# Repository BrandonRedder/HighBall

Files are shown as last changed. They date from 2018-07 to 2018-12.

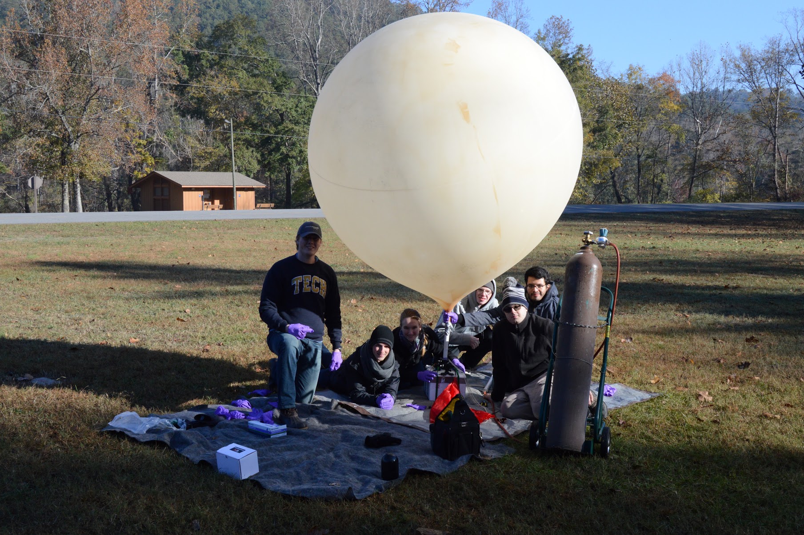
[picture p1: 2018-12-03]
Website/images/DSC_0252.JPG

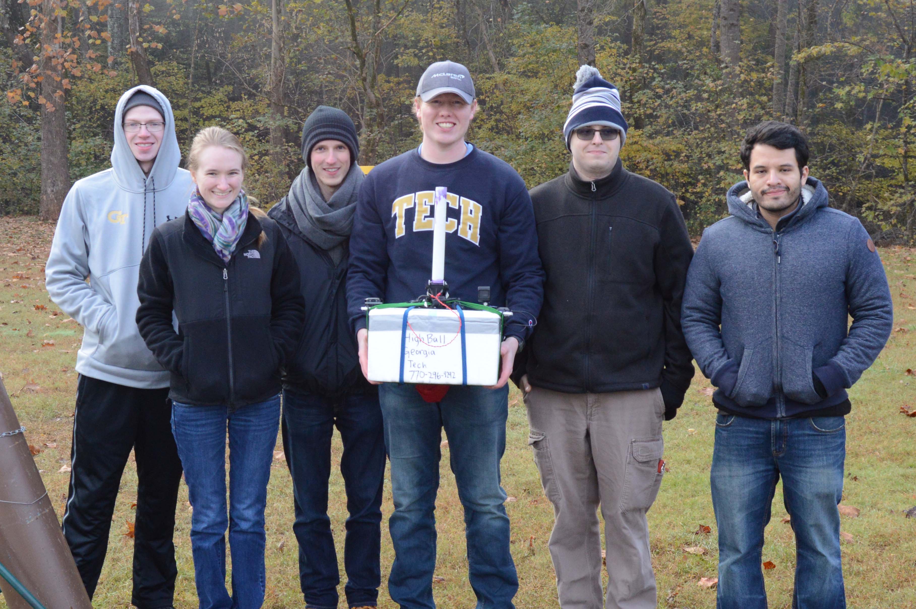
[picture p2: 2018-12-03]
Website/images/DSC_0246.jpg

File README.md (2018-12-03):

# High Ball  
The MITLL High Ball team’s directive is to design, launch, and control a high altitude balloon (HAB). A control system will use varying wind currents at different altitudes to adjust the balloon’s position. The High Ball team is requesting $1000 for development and testing of a viable HAB control system.

## Team Makeup
### Group Members  
* Mathew Manning
* Brandon Redder
* David Richardson
* David Sanchez
* Kristy Scott
* Kyle Watters

### Project Sponsor and Advisors  
**Sponsor:** MIT Lincoln Laboratories  
**Point of Contact:** Navid Yazdani  

**Primary Advisor:** Dr. Morris Cohen  
**Additional Advisor:** Dr. Whit Smith

## Project Goal
The goal of this project is to develop an altitude and location control system 
for a latex HAB to allow long duration flights over a general location. 
Algorithms take into account current pressure and temperature conditions when 
venting helium or dropping ballast to estimate altitude changes. This will
allow for inexpensive controlled balloon flights for a variety of payloads.

## Libraries
* Pressure Sensor (https://github.com/sparkfun/SparkFun_MS5803-14BA_Breakout_Arduino_Library)
* GPS (https://github.com/sparkfun/SparkFun_I2C_GPS_Arduino_Library)
* TinyGPS++ (http://arduiniana.org/libraries/tinygpsplus/)
* IMU (https://github.com/sparkfun/SparkFun_MPU-9250-DMP_Arduino_Library)

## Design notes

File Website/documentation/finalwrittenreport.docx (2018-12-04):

Autonomous Position and Altitude Control System for High Altitude Balloons

ECE4012 Senior Design Project

Section L03, High Ball

Project Advisor, Dr. Cohen

Manning, Mathew W, mathew@gatech.edu

Redder, Brandon A, brandonr@gatech.edu

Richardson, David K, drichardson42@gatech.edu, Team Leader

Sanchez, David, dsanchez36@gatech.edu

Scott, Kristine L, kscott43@gatech.edu

Watters, Kyle, kwatters6@gatech.edu

Submitted

2018 December 4

Executive Summary

The Georgia Institute of Technology in collaboration with the Massachusetts Institute of Technology Lincoln Laboratory developed a low-cost control system for high altitude balloons (HABs). There has been substantial interest in the application of HABs in communication and monitoring of regions not served by traditional infrastructure. Several examples include disaster recovery scenarios, rural areas, and active conflict regions. Many HAB designs suffer from short flight durations, prohibitive cost, or lack position control. The developed system employed a low cost altitude control system to increase flight duration. The payload weighed under six pounds to minimize the regulatory burden and allow the balloon to be operated during inclement weather conditions. In order to keep the design under the weight limit and improve structural stability, a novel cutdown mechanism was developed. To maximize flight duration and regional coverage, an altitude control system was developed using mechanical methods to release helium and ballast as well as a control algorithm. The control algorithm and ballast release have been demonstrated as functioning, but the helium release mechanism will need to be modified for future work. This altitude control could be used in conjunction with wind measurements to provide a position control system in the future. The development cost for the design was $77,117.24 with the cost of hardware per payload being $1,772.94.
Table of Contents

Executive Summary ii

1 Introduction 1
  1.1 Objective 1
  1.2 Motivation 2
  1.3 Background 2
2 Project Description and Goals 3
3 Technical Specifications & Verification 4
4 Design Approach and Details 5
  4.1 Design Approach 5
  4.2 Codes and Standards 17
  4.3 Constraints, Alternatives, and Tradeoffs 19
5 Schedule, Tasks, and Milestones 20
6 Final Project Demonstration 21
7 Marketing and Cost Analysis 25
  7.1 Marketing Analysis 25
  7.2 Cost Analysis 25
8 Conclusion 29
9 Leadership Roles 30
10 References 32

Appendices 36

Autonomous Position and Altitude Control System for High Altitude Balloons

1. Introduction

The MITLL High Ball team’s directive was to design, launch, and control a high altitude balloon (HAB). The control system utilized helium and ballast release mechanisms in order to adjust the balloons altitude. The High Ball team requested $1000 for the development and testing of a viable HAB control system.

  1.1 Objective

The goal of this project was to develop an altitude and location control system for a latex HAB to allow long duration flights over a general location. The control algorithm took into account the balloons altitude and vertical velocity to determine when to release helium or ballast. The altitude change due to dropping ballast was estimated using a simulation which employed the balloon’s lift force and payload weight. Weather forecasts from the National Oceanic and Atmospheric Administration provided wind speeds at distinct pressure levels allowing for prediction of horizontal movement over time [1]. This data was used to develop a model for the projected flight path under various control algorithms.

  1.2 Motivation

High altitude balloons offer a low cost solution for deploying RF and sensor packages. Traditionally, the flight time of an HAB is limited by the balloon bursting. Altitude control systems can drastically improve the flight duration resulting in a larger variety of applications. The presented control system will allow for prolonged deployment over a specific region.

Project Loon, a balloon system developed by Google, uses tennis court sized balloons to provide cellular service to low population regions. These balloons are capable of multi-month flights with both altitude and location control [2]. Although this system has proven to perform well, it is prohibitively expensive for many applications. A similar position control system deployed on a latex balloon will provide a low cost alternative.

  1.3 Background

As latex HABs rise, the decreasing air pressure causes the balloon to expand until the balloon bursts, ending the flight. Flight times are limited to approximately 3 hours. To overcome this hurdle, zero-pressure and super pressure balloons have been designed to increase flight durations. Both balloon types utilize polyethylene film which has a lower elasticity than latex to minimize expansion [3]. Zero-pressure balloons must drop ballast or vent helium to maintain altitude during diurnal cycles, and they can carry loads of up to 6,000 lbs for flights lasting 7-15 days on average [3]. Super pressure balloons rely on a thicker more rigid film material to limit expansion due to changing temperatures, and they can carry loads of up to 2000 lbs for flights lasting over 100 days [3]. For smaller organizations with instrument packages on the scale of 6 lbs these balloon options are unrealistic.

ValBal is a project out of Stanford that produced an altitude control system for latex balloons. The ValBal system holds the current world record for latex balloon flight duration, 121.5 hours [4]. The current design weighs approximately 2.5 kg without ballast and uses a 1500 g balloon with 9 kg of lift allowing the user to include 5 kg of ballast and instruments [4]. Each payload costs $1000 which makes it viable for a much broader range of users [4].

2. Project Description and Goals

The goal was to design a location control system to be used with HABs. Due to time constraints, the design was limited to controlling altitude and relying on the user to manually adjust for varying wind currents. The altitude control system consisted of pressure sensors for determining altitude as well as a mechanical release method for ballast and helium. Motion and location of the balloon was monitored through the use of GPS. An Arduino Mega 2560 was used for data processing and control of mechanical components. The system was deployed in a single payload so that an additional payload may be attached. The second payload could be used for RF or sensing applications. System features include the following:

- Physical control mechanism for helium and ballast release
- Altitude determination through pressure sensor calculations
- Position determination through GPS monitoring
- Manual control of HAB from ground station
- Autonomous HAB flight
- Recoverable payload
3. Technical Specifications & Verification

Table 1. Technical Specifications

Feature | Specifications | Measured Results
Operating Voltages | 3.3v, 5v | 3.3V, 5V
Battery Capacity | 21000 mAh | At least 3.5 hours
Payload Weight | 2500 g | 2245.282 g
Ballast Weight | 220 g | 340.194 g
Operating Altitude | 18 km to 27.4 km | < 4.5 km
Ambient Operating Temperature | -60℃ to 40℃ | Functional at -14.7℃ based on altitude
Internal Operating Temperature | -35℃ to 40℃ | 3.5℃ to 19.5℃
Operating Pressure | 1.0 to 1000.0 hPa | 589.0 hPa to 994.5 hPa
Maximum Recoverable Drop Velocity | 7 m/s | At least 4.27 m/s
Water Resistance | IPX4 | Untested
Flight Duration | 24 hours | 2.5 Hours

Table 2. Communications Specifications

Feature | Specifications | Measured Results
Latency | 5 seconds (for message <70 bytes) | 47.8 seconds
Maximum Usable Distance | Global | Confirmed at 25 miles

4. Design Approach and Details
  4.1 Design Approach
    4.1.1 Mechanical Design

Ballast Release

Ballast was dispensed via a rotary mechanism from the base of the payload. The dispenser assembly consisted of 3D printed parts which operated similar to a gumball machine. A 3D rendering of the design is shown in Figure 1. A set amount of ballast first moves from a chamber in the payload to the hopper. The hopper is then rotated 90° causing the ballast to fall out of the hopper. This rotation also allows ballast to fill the next section of the hopper to be used for the next release. This mechanism prevents a direct connection from the ballast chamber to the exterior of the payload. The hopper was connected to a servo which controlled the number of rotations.

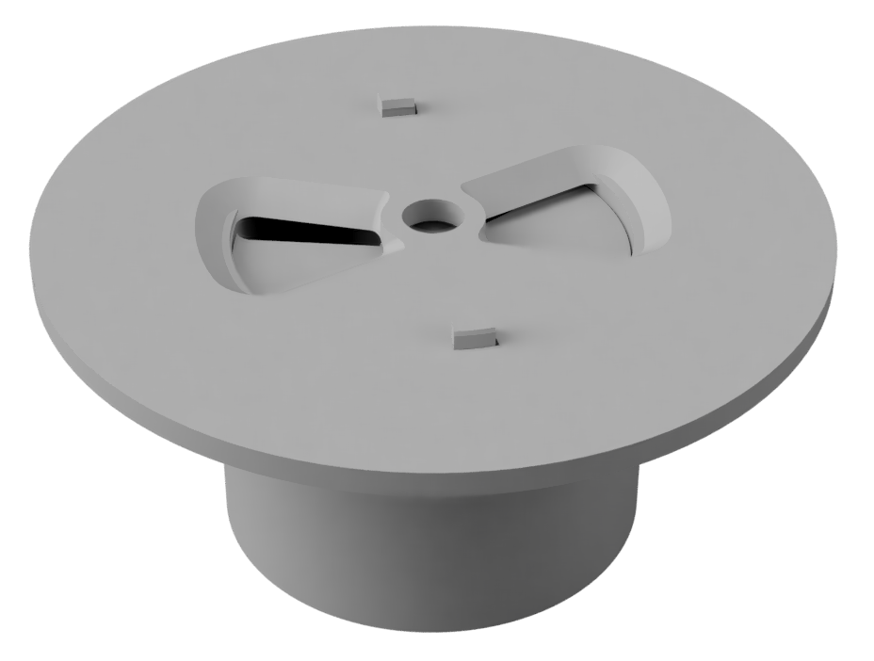
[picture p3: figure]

Figure 1. 3D rendering of the ballast dispenser assembly

Helium Venting

Traditional HABs are connected to their payload by a long cord, but this prevents helium from being released from the balloon. The payload was mechanically connected to the balloon via PVC pipe attached to a mounting bracket on the top of the payload. The balloon was attached to the PVC pipe using zip ties. The PVC is attached to the mounting bracket using an adaptor with two protruding fins that are locked into place by clamps on the mounting bracket. These clamps are held in place using nylon cord. A rubber stopper attached to a spring at the bottom of the bracket blocks the adapter vent to prevent helium from escaping during normal operation. The assembly can be seen in Figure 2. The stopper is attached to a servo located within the payload by a thin rod allowing the servo to open or close the vent. During the flight, a leak was developed. It is uncertain the exact cause, but some potential causes are as follows:

1. The mount and stopper were slightly porous to helium. Helium is a very difficult gas to trap successfully, so it is possible the 3D printed parts were allowing the helium to leak through them.
2. The stopper was not fully sealed against the opening allowing small amounts of gas to escape over the duration of the flight. Once the balloon was attached, it was impossible to check if the stopper was pressed firmly against the opening.
3. There was a non-stopper related hardware failure. This could include the connection between the balloon and the PVC allowing helium to escape, or small cracks in the PVC or mounting bracket.

Further examination and testing is required to determine the exact cause of failure. This is a key flaw in the design that needs to be addressed in future work.

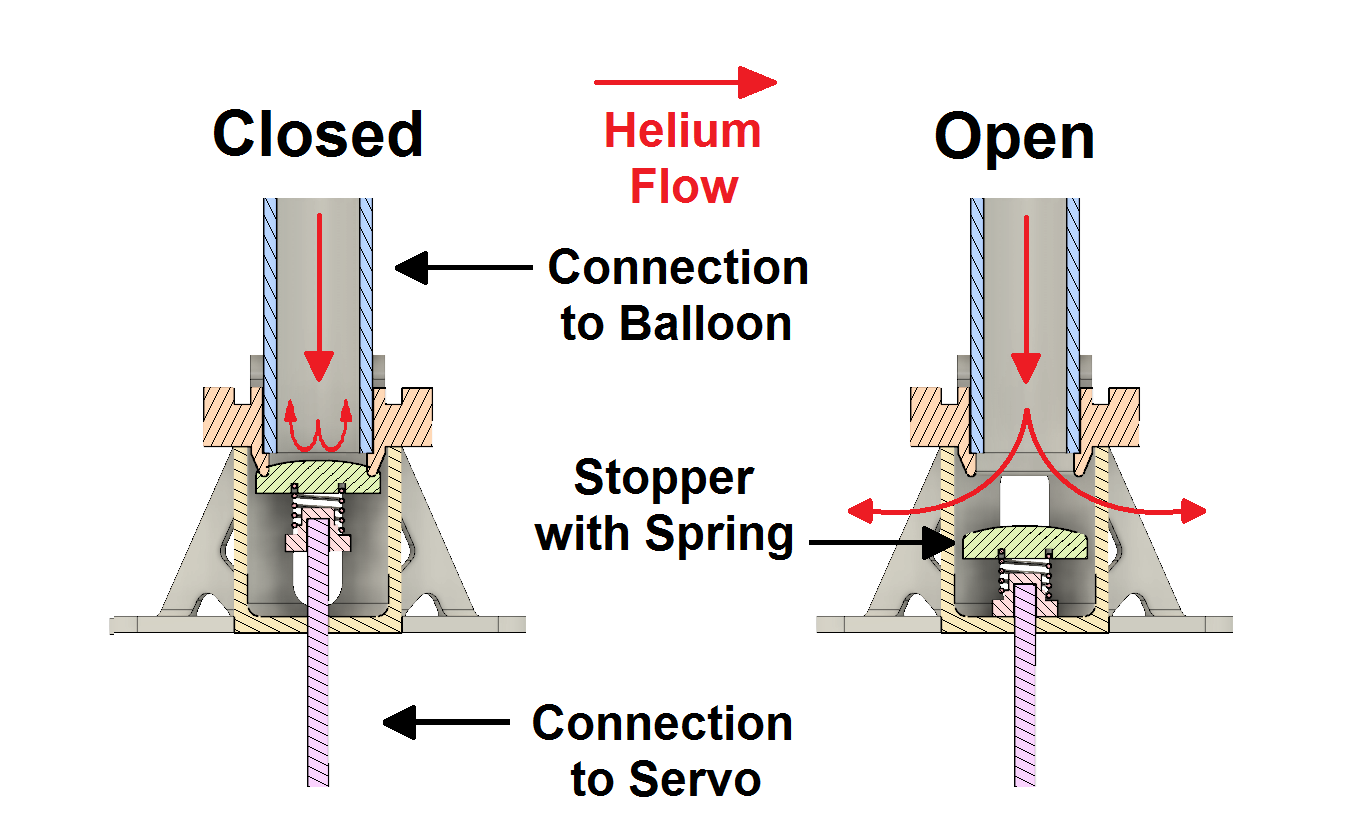
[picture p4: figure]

Figure 2. Helium Venting System

Cutdown

The balloon was rigidly connected to the payload through the helium venting assembly described above. This connection was held in place with a small section of nylon cord as discussed above. Nichrome heater wire was wrapped around the cord similarly to a solenoid. This wrapping can be seen in Figure 3.

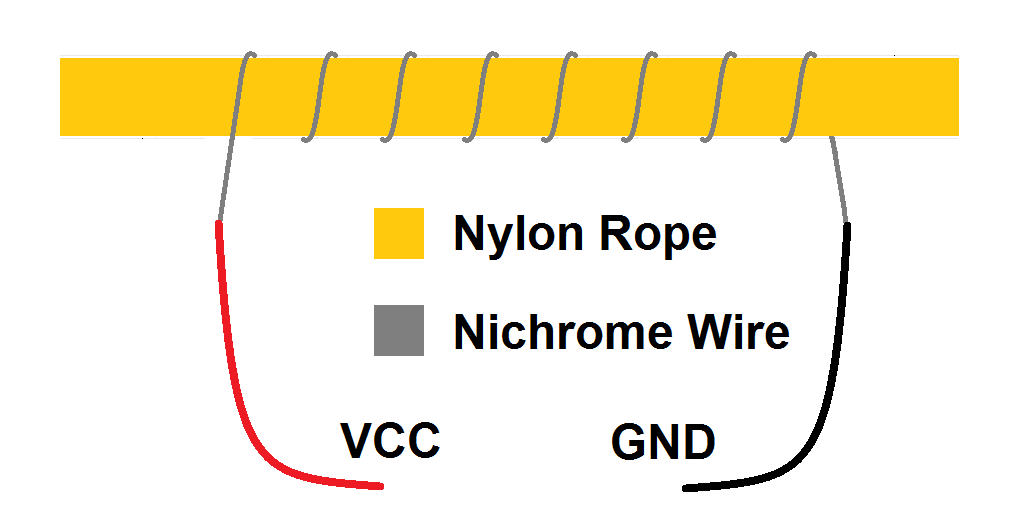
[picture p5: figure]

Figure 3. Nichrome wire wrapped around nylon cord

When the cutdown command is given, the controller biases an N-channel mosfet driver energizing the nichrome wire. This bypasses the voltage regulation circuitry and provides a direct connection from the battery to the nichrome. To control current, the driver is connected to a pulse width modulation pin on the controller. This mechanism, shown in Figure 4, was tested prior to launch and shown to work under the weight of the payload while empty. A video of this test can be seen in Appendix A.

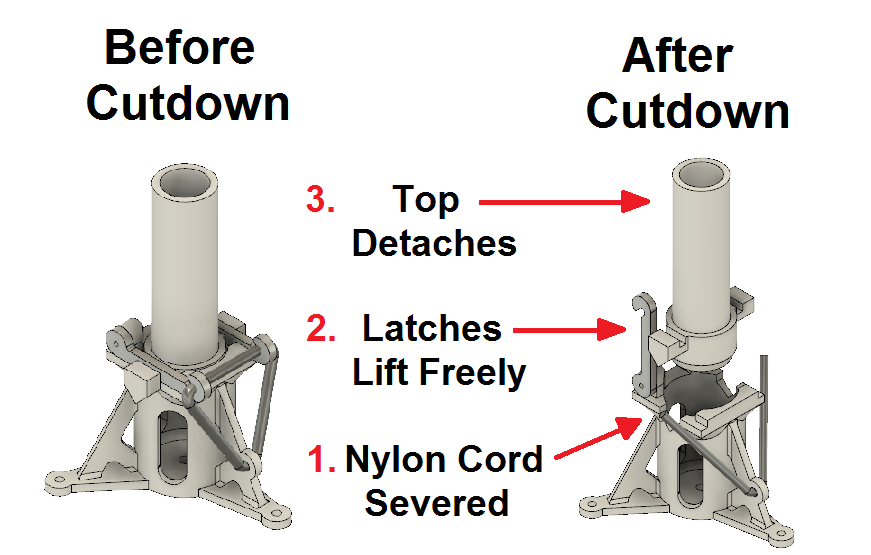
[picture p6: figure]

Figure 4. Cutdown Mechanism

Parachute Deployment

Due to the direct connect between the payload and the balloon, the traditional method of an inline parachute was impossible. The parachute was instead attached to the helium release mounting bracket. With no method of keeping the parachute above the payload, it will fall below and begin to fill with ballast as it is released. To counteract this, a carbon fiber rod was attached to the top of the payload. The parachute was then held to this rod via a plastic loop on the top of the parachute. This prevents the parachute from trailing under the payload while still allowing the parachute to deploy. A video of the drop test can be seen in Appendix A.

    4.1.2 Electrical Design

Communication

Communications between the balloon and the ground station are facilitated through the Iridium satellite network by the RockBlock 9603, a breakout board utilizing the Iridium 9603 satellite transceiver. The breakout board utilizes four communications pins to interact with the microcontroller. The first two pins are RX and TX connections to allow messages to be sent to and from the device. The other 2 pins allow the RockBlock board to be placed in a low power state to preserve energy and to inform the microcontroller when a new message has arrived. The module uses an external 1621 Mhz patch antenna to communicate with satellites [5]. Outgoing messages are rerouted through nearby satellites before being sent to an Iridium ground station where the message is sent via an email attachment to the user [5]. Incoming messages are uploaded as an HTTP POST to the RockBlock website before being sent back through the same channels to the transceiver.

Microcontroller

The microcontroller used was the Arduino Mega 2560 development board (based on the ATmega2560). It was selected due to being available from the previous development team. It fit the communication and use requirements for managing the payload. Using a smaller board is possible if size or weight becomes a significant limiting factor, but at only 37g, the Arduino mega is not a significant source of weight [6]. The microcontroller is connected to the remainder of the electronic components via a custom PCB.

Sensors

Several sensors were used to provide data to the controller. In addition, some sensors were removed from the design due to technical constraints. The code for reading the data from the sensors is included in Appendix B (Sensors.cpp and Sensor.h). Each of the sensors are summarized below.

GPS Module

The GPS module used was the SparkFun XA1110 GPS [7]. This module was selected specifically due to its “balloon mode” which allows it to continue functioning above 65,000 feet. This was the primary method of monitoring the position of the balloon.

The GPS altitude is also sent to the ground station and displayed on the graphical user interface (GUI). This altitude was not used in the control algorithm due to the limitations of GPS altitude measurements [8]. Instead the altitude measured from the altimeters was used.

Altimeters (2x)

The altimeters used were the SparkFun Pressure Sensor Breakout - MS5803-14BA [9]. This sensor was selected due to the ease of integration, and its pressure range of 0-14 bar with a minimum resolution of 0.2 mbar. At altitudes of 70-90 thousand feet, the atmospheric pressure is 17.6-44.9 mbar [10]. Since altitude determination was the basis of the control algorithm, two altimeters were included in the design to mitigate any potential for sensor failure. Due to time constraints, no sensor failure detection was implemented in the code. Instead, the measurements from the two sensors were averaged. Future work should include more robust failure detection which can be done by comparing to the GPS altitude or an expected value.

Temperature Sensor - Removed

The temperature sensor initially specified in the design was the TI LM335Z/NOPB [11]. This sensor was specified due to its range overlap (-40 to 100 °C) with the temperatures expected at altitude. Originally, the temperature sensor was to be used as a control for an internal heating element. To preserve battery and reach the desired temperature the heater was going to be turned on and off. It was ultimately removed from the design as the electronics were estimated to produce enough heat to stay within the operating temperature range. For monitoring of the payload conditions, temperature data was sent to the ground.

During testing, the temperature sensor was reading inaccurate and inconsistent data. This may have been due to a hardware fault earlier in the semester, but the cause of failure was not determined. This led to the removal of the temperature sensor from the design. In its place, the pressure sensors’ built in temperature sensors were used which have an accuracy of ±0.8℃ [9]. For internal temperature monitoring, this was determined to be sufficiently accurate; however, if future work needs more accurate temperature measurements, a dedicated temperature sensor should be added back to the design.

Inertial Measurement Unit (IMU) - Removed

The IMU initially specified in the design was the SparkFun 9DoF Razor IMU M0 [12]. This sensor was intended to be used to calculate acceleration both normal and tangential to Earth as well as provide a check for the altitude and position measurements. Unfortunately, the selected IMU presented significant software challenges. While an IMU provides valuable information for position monitoring, future designs should use a different IMU. The issues with the presented IMU are outlined below:

1. The x, y, and z axes for the acceleration measurements differed from what was printed on the board. Per the datasheet, the axis orientation for the compass outputs differs from that of the accelerometer and gyroscope outputs, and the printed axes correspond to the compass. To avoid confusion, the following changes were made to the acceleration outputs to match the axes printed on the board: x acceleration to the y axis, y acceleration to the x axis, and z acceleration to the -z axis.
2. The provided repository for the chip had errors calculating roll, pitch, and yaw. This required changes to the firmware on the internal microprocessor to account for these differences. The current state of the firmware is shown in Appendix C.
3. Communication between the IMU on-board Arduino and the primary Arduino MEGA was unsuccessful. This is what led to the IMU’s removal from the final design.

In addition to the above mentioned issues, future work should aim to make the code robust to initial position upon powering on the IMU. The sensor outputs are relative to the initial position rather than absolute measurements. The current design requires the IMU be in a specific orientation when turning on. The IMU must be level with the x axis pointing north for determining the vertical and tangential directions respectively. Future designs should use the acceleration due to gravity to find the true vertical direction and the magnetometer to find the true tangential direction. This will provide more accurate data and prevent any errors due to misalignment when turning on the device.

    4.1.3 Software

Ground Station Interface

The ground station interface consists of a GUI which allows the user to compile new messages, view previously sent messages or received messages, and view real time graphs of received data. As the payload sends messages to the ground, that information is retrieved automatically and the GUI displays an incoming message notification. Each new message contains the balloon’s GPS coordinates, altitude, interior temperature, and pressure measurements along with current software settings. Outgoing messages contain specifications for the altitude control algorithm and manual commands for venting helium, dropping ballast, and cutting down the payload. The layout of the main GUI tab can be seen in Figure 5. For brevity, the layout of each page of the GUI and the code for the GUI can be found in Appendix D and E respectively.

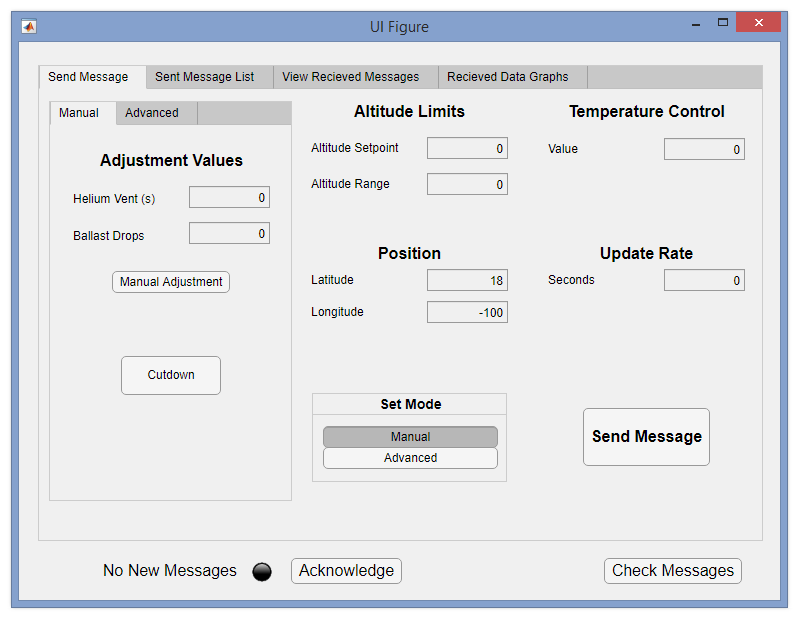
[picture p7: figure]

Figure 5. GUI Main Page

Altitude Control

The altitude control system was separated into three subsystems, the helium release, the ballast release, and the autonomous control loop. The software for the helium and ballast release can be seen in Appendix B (Actuators.cpp and Actuators.h). To control the helium and ballast release, servos were rotated a specified amount to either open/close the helium vent or release a set of ballast. These functions could be triggered either by the autonomous control or by communication from the ground station. The code for the autonomous control loop can also be seen in Appendix B (Control.cpp and Control.h). Both the altitude and vertical velocity were weighted in order to determine when to release helium or ballast. These weights were determined using a simulation. Initially, the algorithm was intended to use the vertical acceleration found by the IMU, but due to the removal of the IMU, the vertical acceleration was also removed. A simulation of the control algorithm showed that the removal of the vertical acceleration had a negligible impact on the effectiveness of the algorithm.

Issues and Considerations

In its current state, the payload must be launched in manual control mode. This is because the altitude control loop has no guard on releasing ballast if the balloon was just launched. As a proof of concept, this functionality works, but future work should aim to allow for fully autonomous flight from launch to landing. A similar guard should be placed on the helium release while the payload is falling in order to reduce battery consumption.

Future work can also be done to improve the control loop. The weights for the different parameters can be optimized based on measured helium release rates. There may also be additional parameters that play a key role in how the balloon operates such as temperature or wind conditions that are not currently accounted for. Additionally, for longer flights, it may be possible to use the natural warming and cooling of the atmosphere to prolong the flight.

Iridium Communication

Messages to and from the balloon are in the form of a segmented binary vector. Each segment is a predetermined length and represents a different parameter. To limit overall data usage the minimum and maximum values of each parameter were determined along with the resolution of the sensors involved. This allows the parameter to be represented as an integer value with the following formula; Encoded =Round((Value - Minimum)/(Resolution)) . The encoded value will be an unsigned integer with a minimum value of 0 and a known maximum value, meaning only N bits are needed to store the value without losing precision given Maximum ≤ 2^N . Figure 6a shows the layout of messages sent to the payload and Figure 6b shows the layout of messages received from the payload. Functions were developed for both the microcontroller and the ground station to encode and decode messages using this predetermined structure. The code for the communication can be seen in Appendix B (Communications.h and Communications.cpp).

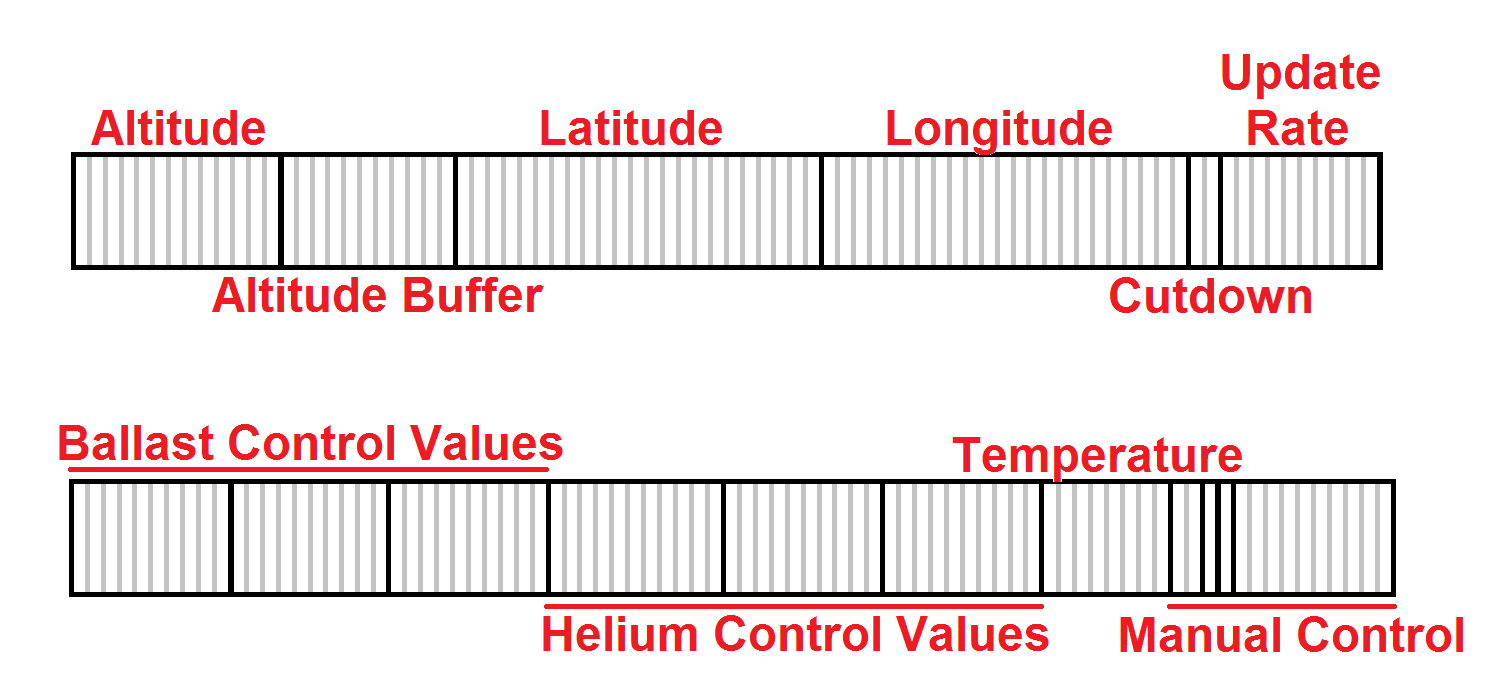
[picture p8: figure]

Figure 6a. Message Structure from Ground to Payload

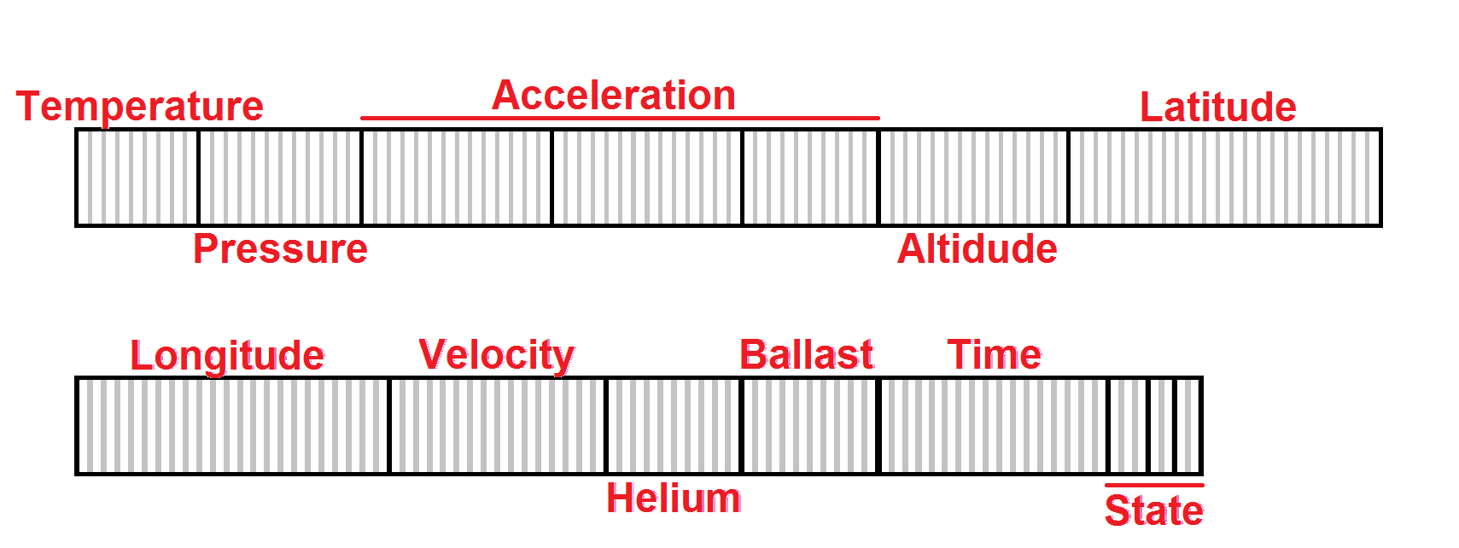
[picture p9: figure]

Figure 6b. Message Structure from Payload to Ground

Flight Simulation

Current HAB flight simulation tools operate on the assumption that the balloon rises until it pops then begins falling. This does not provide an accurate model when the payload is actively preventing the balloon from reaching the altitude at which the balloon pops. To circumvent this, a flight simulation tool was developed. This model utilizes weather data from the Global Forecasting System [1] to determine the wind conditions, pressure, humidity, and temperature at a given time and position. The data is used to determine the buoyancy, drag, and gravitational forces acting on the balloons given the current velocity, mass of the payload, and mass of helium in the balloon. These forces allow the balloon’s instantaneous acceleration to be approximated over time, even when changes to the system occur during helium venting or dropping ballast. The simulation outputs the ambient weather conditions, position, acceleration and velocity of the payload which can be viewed graphically. The simulation ends when the payload reaches the ground or when a preset time is reached. While the simulation cannot account for all variables, it allows the user to approximate how the balloon’s trajectory will change in response to the altitude control system. This was utilized to determine appropriate variables for the control algorithm. The full flight simulation code can be seen in Appendix F.

Temperature Control

Temperature control was omitted in the final design due to the short expected duration of the flight. For short flights, the heat generated by the electrical components provides sufficient heat to keep the interior temperature above the operating range. This may not be the case for longer duration flights. If that is the case, a heating element can be added to the design to maintain the internal temperature.

Wind Detection

Due to time constraints, wind detection was not implemented in the design. This prevents the design from autonomously adjusting position, but it is still possible through manual changes from the ground station. This requires the person at the ground station to determine the wind conditions from the available data and correctly send helium or ballast release commands. Future work should aim to determine wind direction on board to allow for autonomous position control. This may require an IMU to monitor the payload’s orientation and horizontal acceleration.

  4.2 Codes and Standards

FAA Title 14 - Part 101 - Subpart A (Appendix G) describes the conditions under which unmanned civilian vehicles may be operated within the United States. Part 101.1 specifies that any unmanned free balloon must comply with subpart D with the exception of balloons that:

- Carries a payload package that weighs more than four pounds and has a weight/size ratio of more than three ounces per square inch on any surface of the package, determined by dividing the total weight in ounces of the payload package by the area in square inches of its smallest surface
- Carries a payload package that weighs more than six pounds
- Carries a payload of two or more packages that weighs more than 12 pounds
- Uses a rope or other device for suspension of the payload that requires an impact force of more than 50 pounds to separate the suspended payload from the balloon

The regulations in Subpart D (Appendix H) directly interfere with the intended application of the system, so the payload is designed to comply with the exceptions listed in Part 101.1.

Part 101.7, as it applies to unmanned free balloons, prohibits the operation of the balloon in a manner that may be hazardous to other persons, or their property. It also prohibits dropping any objects, if such an action creates a hazard [13].

FCC Title 47 - Part 97.113 lists prohibited transmissions on amateur radio wavelengths. Relating to this project, no station shall transmit communications for hire or for material compensation, direct or indirect, paid or promised, except as otherwise provided in these rules [14]. This regulation makes amatueur radio an unsuitable means of communication for the system due to the commercial nature of the project.

FCC Title 47 - Part 22.925 prohibits the use of cellular phones while airborne, preventing the system from using a cellular phone to communicate with the payload during flight [15].

The Iridium 9603 transceiver utilized in this design has been granted authorization by the FCC as a Licensed Non-Broadcast Station Transmitter under the conditions listed in FCC Title 47 - Part 25 [16]. The grant of equipment authorization requires that the transmitter be installed to provide 20 cm of separation distance from all persons, and must not be operation in conjunction with any other transmitter within a host device [17].

  4.3 Constraints, Alternatives, and Tradeoffs

Due to FAA regulations, the payload weight must be less than 6 lbs [13]. This restriction resulted in a tradeoff between component selection and ballast weight. Maximizing the amount of ballast is important for increasing flight duration, but longer flights require a larger power supply. The structure for the payload also contributed to the weight because it had to be sturdy enough to hold the cutoff mechanism for the balloon and provide insulation. Though greatly reduced through iterative design, the weight of this housing was a large portion of the total weight. The current design opted to increase structural rigidity instead of increasing flight duration. This decision was made to improve the chances of payload recovery, and to show a proof of concept for the altitude control mechanisms.

Due to the altitude of HAB flights, the system must be able to sustain operations in temperatures as low as -60° C. Many electronic components fail at this temperature, so special considerations were taken into account when designing the payload. The enclosure used was insulated so that less heat would be lost, and the heat generated by the electronics on the inside helped maintain internal temperature. The heater originally proposed was not used due to reasons discussed in Section 4.1.3. The test flight did not reach an altitude at which the internal temperature could be tested, so it is not currently known if a heater is necessary. The payload remained in the operating temperature during the test flight. The lowest recorded internal temperature was 3.5℃, measured while the lid was open prior to launch. During the flight, the internal temperature steadily rose due to the heat generated by the electrical components.

5. Schedule, Tasks, and Milestones

The GANTT and PERT chart are shown below in Appendix I and J respectively.

Brandon Redder performed the majority of the payload hardware design and assembly. He also did the PCB design and fabrication. The hardware assembly was a critical element, and the last thing completed on the critical path. Mathew Manning helped Brandon with hardware assembly and testing. Mathew’s tasking played an important role in meeting deadlines and ensuring all elements of the hardware were functioning. David Richardson wrote and maintained the control algorithm and all the sensor interfaces except the IMU. He assisted with the IMU calculations, and worked on the communication between the main Arduino and the IMU. Additionally, he was involved in the testing and debugging of both hardware and software. These tasks were on the critical path and were of medium complexity. The primary source of difficulty was with the IMU communication and software debugging. Kristine Scott wrote the firmware for the IMU to calculate acceleration and orientation values. She also assisted with software, and communication debugging. Although the IMU was removed from the design, it was a difficult task that took a significant amount of time. Her assistance with debugging was also important to the launch of the payload on time. David Sanchez developed the day of launch checklist, as well as determining a location to launch from. While this tasking was fairly simple, it took time and was one of the most important tasks of the project. He also played a significant role in the cutdown code and testing as well as debugging of the software. His testing of the GPS caught a significant error in the code that would have resulted in data loss at high altitude. Kyle Watters wrote both the simulation and communication code for the project. Communication with the payload was one of the most critical features of the design, as without it there would be no way to test any of the other design elements. This in conjunction with the simulation code posed a moderately difficult task that took a considerable amount of time. The main loop was written by David R., Kristine, David S., and Kyle. This was the most critical piece of software in the design but was of relatively low difficulty.

6. Final Project Demonstration

The final project demonstration was done in two parts, in flight reporting and ground testing. The following specifications were demonstrated during and immediately prior to the flight:

- The hardware was operating at the specified 3.3V and 5V.
- The time from powering on to payload recovery was 3.5 hours which demonstrated a minimum estimate for battery capacity.
- The payload weight was measured to be 2245.282 g which is below the 2500 g limit. This allowed the ballast weight to exceed its specification at 340.194 g.
- The altitude reached 4.5 km during the flight which falls well below the desired range of 18 km to 27.4 km. This was due to a helium leak likely due to a hardware failure as discussed in the Helium Release subsection of §4.1.1. A plot of the altitude vs time can be seen in Figure 7.
- The minimum ambient operating temperature experienced during flight was -14.7℃. Testing at the minimum specified temperature was impossible to the previously mentioned maximum altitude falling below the expected altitude.
- The operating temperature during the flight ranged between 3.5℃ and 19.5℃ which was within the required range. The temperature was shown to increase over the duration of the flight as shown in Figure 8. This indicates the payload may be able to self regulate temperature without an internal heating element.
- The minimum pressure experienced during the flight was 589.0 hPa. The payload remained operational at this pressure, but pressures below that were unable to be tested. A graph of the pressure vs time can be seen in Figure 9.
- The drop velocity was measured to be 4.27 m/s and the payload was fully functional after recovery. This velocity was calculated from the altitude vs time graph shown above in Figure 7.
- Water resistance was untested as it was deemed unnecessary for the initial prototype
- The flight duration accomplished was 2.5 hours.
- Latency was measured to be 47.8 seconds.
- The usable distance for the payload communication was confirmed to be at least 25 miles from the ground station and was consistent when the payload was in view of satellites. After the payload left the ground, the communication was more consistent and reliable than it was on the ground. This is thought to be because there was less blocking the view of the payload.
- The ballast release mechanism was shown to work after the payload had landed, prior to recovery. It was impossible to see if ballast was released during the flight due to a helium leak, but the post landing tests showed that it was working through remote communication.
- Helium release was shown to have an impact on the buoyancy of the balloon and it was shown that the blocking method was not fully functional from the path that the flight took. The effects of this leak can be seen in Figure 7 where the altitude follows the path expected of a continuous loss in lift.

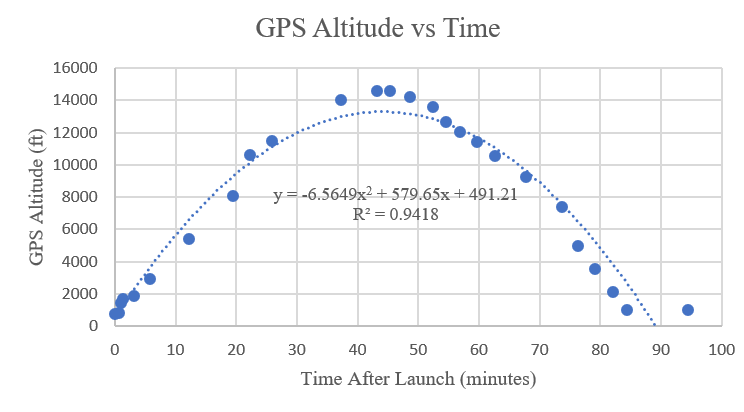
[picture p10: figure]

Figure 7. Plot of balloon altitude vs time from the test flight

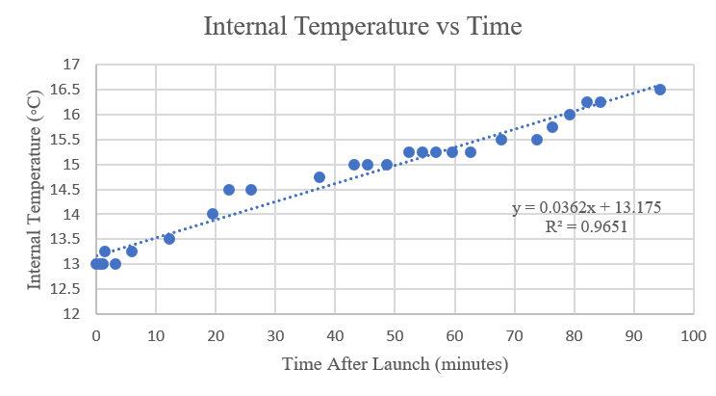
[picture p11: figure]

Figure 8. Plot of payload temperature vs time from the test flight

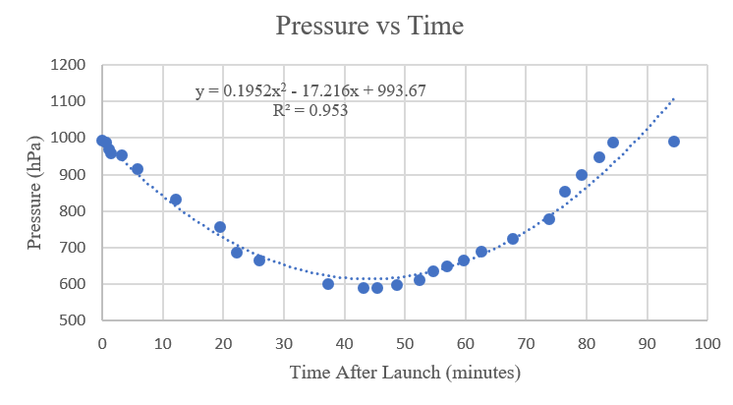
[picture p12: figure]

Figure 9. Plot of pressure vs time from the test flight.

Ground testing demonstrated the functionality of the payload and is as follows:

- The parachute deployment method was tested by a four story drop test. A video of the drop can be seen in Appendix A.
- The cutdown method was tested iteratively so that the best wrapping method for nichrome wire could be determined as well as the effects of cutdown on the other electronic components. The method of wrapping can be seen in the Cutdown subsection of §4.1.1 and the current draw was not enough to affect the other components.
- Ballast dispensing was demonstrated both on the ground and during the flight. The dispensing mechanism was tested on the ground and can be seen in a video in Appendix A.
- The helium venting mechanism was demonstrated to work mechanically, but from the launch, it was shown to be ineffective at blocking the release of helium.
- The physical functionality of the payload demonstrated the functionality of the software and communications. The data being taken can be seen in the logs in Appendix K.
7. Marketing and Cost Analysis
  7.1 Marketing Analysis

It is not plausible to launch an HAB project at the same scale as Project Loon unless adequate funding is acquired [2]. Stanford University's ValBal team developed a low cost alternative. The ValBal project utilized less than $1,000 to achieve the longest recorded latex balloon flight. The Stanford team’s aircraft used an altitude control system to extend the flight duration [18]. In addition to altitude control, the proposed design aimed to develop a position control system. Though the project did not demonstrate autonomous position control. Changing altitude with known wind directions will allow for directed changes in position. The presented work could be easily built upon to develop an autonomous position control system.

The ValBal design exceeds the weight limit specification which requires users to follow FAA regulations 101.33, 101.35, 101.37, and 101.39 [13] [18]. The proposed design weighed less than six pounds which will allowed for an additional six pound payload without needing to follow the above FAA regulations. Of particular importance, the proposed system may be operated during inclement weather conditions without prior notice to the FAA [13].

  7.2 Cost Analysis

7.2.1 Hardware Costs

The HAB control system consisted of electronic, mechanical, and structural components. The previous design effort purchased some supplies that were reused shown in Table 3. These items are listed separately because they were purchased by the previous team. They were included in the final cost calculations.

Table 3. Previous Supplies

Item | Estimated Cost
Arduino Mega 2560 | $38.50
5 ft Diameter Parachute | $50
1200 g Latex Balloon | $120
RockBLOCK Iridium Module | $250
Servos | $80

The additional parts necessary to build the design are listed in Appendix L. The listed components provide enough materials for a single launch. Additional launches will require new balloons and potentially hardware if the payload is unrecoverable.

In addition to hardware, the satellite communication in use requires a data plan with monthly costs and additional charges to purchase credits as shown in Table 4. The credits are needed to send or receive messages with each action costing 1 credit.

Table 5 shows the cost of each of the individual subsystems. An entire bill of materials is included in Appendix L.

Table 4. Communication Data Plan Charges

| Cost per each | Quantity
Monthly Subscription Fee | $12.75 | 3
200 Credits | $25.50 | 1
1000 Credits (Bundle Discount) | $102.02 | 1
Total Cost | $165.78

Table 5. Subsystem Costs

Project Subsystem | Cost
Payload | $231.84
Helium | $250
Electrical System | $371.88
Cutdown | $126.71
Communications | $611.07
Ballast | $181.75
Total | $1,772.94

7.2.2 Development Costs

The design team will consist of six engineers. Table 6 shows the number of work hours per engineer estimated for the duration of the project.

Table 6. Number of Work Hours per Engineer

Task | Hours
Sensor Integration | 13
Algorithm Development and Implementation | 28
Research | 5
Meetings | 15
Parts Fabrication | 15
Assembly | 20
Ground Testing | 10
Launches and Launch Preparation | 15
Presentation | 2
Reports | 12
Total | 135

Each engineer is estimated to have a salary of $65,000, per year [19]. The United States Office of Personnel Management defines one work year as 2087 hours [20]. Using these estimates, the hourly rate of a single engineer is $31.15. A fringe benefit rate of 31.9% and an overhead rate of 120% are assumed [21]. The total development costs under these assumptions are shown in Table 7.

Table 7. Total Project Costs

Project Section | Cost
Parts | $1,607.16
Communication Costs | $165.78
Labor | $25,231.50
Fringe Benefits (31.9% of Labor) | $8,048.85
Subtotal | $35,053.29
Overhead (120% of Subtotal) | $42,063.95
Total | $77,117.24

8. Conclusion

In its current state, the payload is capable of releasing ballast based on manual or automatic control schemes. The helium release mechanism allowed helium to leak over the duration of the flight. While this does demonstrate that the opening was large enough to vent sufficient gas to reduce altitude, it is a significant design flaw that needs to be addressed in future work. In order for the payload to adequately control altitude, a method for preventing the helium from venting unintentionally must be developed. Testing of the control algorithm was also limited due to time constraints and insufficient test flight data. Since the test flight only reached approximately 4.5 km, there was not enough data gathered to provide an accurate model for how to control the balloon. Future flights would provide valuable feedback on how the current control algorithm performs, as well as where potential improvements can be made.

During the development of the payload, certain errors were made that should be avoided during future work. Of particular note, was the selection of an IMU with a separate on board Arduino, and the milling of the custom PCB. Due to the on board Arduino, the team was unable to get communication between the IMU and the main microcontroller. This made determining vertical acceleration impossible which limited the data available to the control algorithm. The removal of the IMU also prevented checking the altitude and position data against the IMU’s acceleration and rotational data as discussed in the initial proposal. In the future, an IMU that connects directly to the main controller would be easier to communicate with and use. When milling the PCB, multiple shorts were developed. This ultimately led to the failure of the GPS and IMU sensors. These components were replaced, but in the future, any PCBs should be examined closely to prevent this from happening. Having the PCB milled by a professional board house would likely reduce the chances of this happening again.

9. Leadership Roles

Brandon Redder was responsible for maintains the group’s website as the webmaster. He also led hardware assembly. Mathew Manning led the recovery team after the payload landed. He also played a key role in the hardware assembly and testing. As team leader, David Richardson oversaw communication between the team and advisors. He provided direction and made final decisions regarding both hardware and software design elements. He is also the expo coordinator for the team. Kristine Scott led the integration of the different sensor elements. She was also the documentation lead, meaning she was responsible for ensuring all documentation was submitted in a timely manner. David Sanchez oversaw pre-launch preparation. This included launch site selection, pre-launch checklists, and ensuring all necessary items were brought to the launch site. He was also the primary contact for the cutdown software implementation. Kyle Waters oversaw both the simulation and satellite communications. In this role, he developed models for the balloon’s flight path, and used this to help define control parameters. He was also responsible for all communication between the payload and ground station.

10. References

[1] National Oceanic and Atmospheric Administration, “Global Forecast System (GFS),” July 14, 2018. [Online]. Available: (https://www.ncdc.noaa.gov/data-access/model-data/model-datasets/global-forcast-system-gfs)https://www.ncdc.noaa.gov/data-access/model-data/model-datasets/global-forcast-system-gfs [Accessed: July 20, 2018].

[2] X Development LLC, “Technology,” Project Loon, 2018, [Online]. Available: (https://loon.co/technology/)https://loon.co/technology/ [Accessed: Jun. 8, 2018].

[3] B. Dunbar, H. Zell, “Types of Balloons”, National Aeronautics and Space Administration, Aug. 3, 2017 [Online]. Available: https://www.nasa.gov/scientific-balloons/types-of-balloons [Accessed July 19, 2018].

[4] Andrey Sushko, Aria Tedjarati, Joan Creus-Costa, Kai Marshland, Paige Brown, Davy Ragland, John Dean, Sasha Maldonado, John M. Pauly, “Advancements in low-cost, long endurance, altitude controlled latex balloons (ValBal),” In Proc. 2018 IEEE Aerospace Conference, 2017 pp. 1-9. [Online]. Available: (https://ieeexplore.ieee.org/document/8396588/)https://ieeexplore.ieee.org/document/8396588/ [Accessed: July 20, 2018].

[5] Rock Seven Location Technology, “RockBlock 9603,” RockBlock 9603 datasheet, [Online]. Available: http://www.rock7mobile.com/downloads/RockBLOCK-9603-Product-Information-Sheet.pdf [Accessed: November 30, 2018]

[6] Arduino, [Online]. Available: https://store.arduino.cc/usa/arduino-mega-2560-rev3 [Accessed: December 2, 2018]

[7] Sparkfun Electronics, “SparkFun GPS Breakout - XA1110 (Qwiic) Hookup Guide,” [Online]. Available: https://learn.sparkfun.com/tutorials/sparkfun-gps-breakout---xa1110-qwiic-hookup-guide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 [Accessed: December 2, 2018]

[8] M. Graham, “GPS Versus Barometric Altitude: The Definitive Answer,” xcmag.com, Jul. 23, 2011. [Online]. Available: http://xcmag.com/news/gps-versus-barometric-altitude-the-definitiveanswer/. [Accessed Dec. 3, 2018].

[9] TE Connectivity, “Miniature 14 bar Module,” MS5803-14BA datasheet, Aug. 2017 [Online]. Available: https://www.te.com/commerce/DocumentDelivery/DDEController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 [Accessed: November 30, 2018]

[10] AVS, “Atmospheric Pressure at Different Altitudes,” avs.org. [Online]. Available: https://www.avs.org/AVS/files/c7/c7edaedb-95b2-438f-adfb-36de54f87b9e.pdf [Accessed Dec. 3, 2018].

[11] Texas Instruments, “LMx35, LMx35A Precision Temperature Sensors,” LM135, LM135A, LM235, LM235A, LM335, LM335A datasheet, May 1999 [Revised Feb. 2015]. Available: http://www.ti.com/lit/ds/symlink/lm335.pdf [Accessed: November 30, 2018]

[12] Sparkfun Electronics, “9DoF Razor IMU M0 Hookup Guide,” [Online]. Available:

https://learn.sparkfun.com/tutorials/9dof-razor-imu-m0-hookup-guide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 [Accessed: December 2, 2018]

[13] Code of Federal Regulations Title 14 Part 101 (14CFR101), Moored Balloons, Kites, Amateur Rockets, Unmanned Free Balloons, and Certain Model Aircraft [Online]. Available: (https://ecfr.io/Title-14/pt14.2.101)https://ecfr.io/Title-14/pt14.2.101#sp14.2.101 [Accessed: July 19, 2018].

[14] Code of Federal Regulations Title 47 Part 97.113, Amateur Radio Service, Prohibited Transmissions [Online]. Available: (https://ecfr.io/Title-47/se47.5.97_1113)https://ecfr.io/Title-47/se47.5.97_1113 [Accessed: July 19, 2018].

[15] Code of Federal Regulations Title 47 Part 22.925, Public Mobile Services, Prohibition on Airborne Operation of Cellular Telephones [Online]. Available: (https://ecfr.io/Title-47/pt47.2.22)https://ecfr.io/Title-47/pt47.2.22#se47.2.22_1925 [Accessed: July 19, 2018].

[16] Code of Federal Regulations Title 47 Part 25, Satellite Communications [Online]. Available: (https://ecfr.io/Title-47/pt47.2.25)https://ecfr.io/Title-47/pt47.2.25 [Accessed: July 19, 2018].

[17] Iridium Communications Inc, “Iridium 9603 Short Burst Data Modem: Declaration of Conformity,” Iridium Short Burst Data (SBD), July 19, 2018. [Online]. Available: (https://www.iridium.com/file/24245/)https://www.iridium.com/file/24245/ [Accessed: July 20, 2018].

[18] A. Sushko, A. Tedjarati, J. Crues-Costa, S. Maldonado, K. Marshland, and M. Pavone, “Low Cost, High Endurance, Altitude-Controlled Latex Balloon for Near-Space Research (ValBal),” In Proc. IEEE Aerospace Conference ’03, 2017, pp. 1-9. [Online]. Available: (http://ieeexplore.ieee.org/stamp/stamp.jsp?tp=&arnumber=7943912&isnumber=7943554)http://ieeexplore.ieee.org/stamp/stamp.jsp?tp=&arnumber=7943912&isnumber=7943554 [Accessed: July 20, 2018].

[19] Georgia Tech School of Electrical and Computer Engineering, “What is ECE at Georgia Tech,” Georgia Institute of Technology, 2018. para. 11, Apr. 4, 2018 [Online]. Available: (https://www.ece.gatech.edu/what-ece-georgia-tech)https://www.ece.gatech.edu/what-ece-georgia-tech [Accessed July 19, 2018].

[20] US Office of Personnel Management, “ Pay & Leave: Pay Administration,” OPM.gov, para. 1. [Online]. Available: (https://www.opm.gov/policy-data-oversight/pay-leave/pay-administration/fact-sheets/computing-hourly-rates-of-pay-using-the-2087-hour-divisor/)https://www.opm.gov/policy-data-oversight/pay-leave/pay-administration/fact-sheets/computing-hourly-rates-of-pay-using-the-2087-hour-divisor/ [Accessed: July 19, 2018].

[21] Georgia Tech Office of Sponsored Programs, “Facilities & Administrative Rates,” Georgia Tech Office of Sponsored Programs, para. 3, July 6, 2018. [Online]. Available: (http://www.osp.gatech.edu/rates)http://www.osp.gatech.edu/rates [Accessed: July 19, 2018].

Appendix A

This appendix contains a collection of videos showing testing procedure for the cutdown mechanism as well as the ballast and helium release system.

The videos are linked from our website located at: www.HighBallSeniorDesign.com/project_documentation.html

They can also be directly accessed from here:

https://photos.app.goo.gl/7F5YTKmhSC1EK4um7

Appendix B

This appendix contains the source code for the main payload Arduino Mega.

The code is located on a public GitHub linked from our site: www.HighBallSeniorDesign.com/project_documentation.html

It can also be accessed directly here: https://github.com/BrandonRedder/HighBall/tree/master/Software/Control%20Payload/Control%20Payload%200-1/Payload_Main

Appendix C

This appendix contains the source code for the IMU’s Arduino SAMD.

The code is located on a public GitHub linked from our site: www.HighBallSeniorDesign.com/project_documentation.html

It can also be accessed directly here:

https://github.com/BrandonRedder/HighBall/tree/master/Software/IMU

Appendix D

This appendix contains screenshot of each page of the communication and control GUI.

The screenshots are stored on in a Google Photos album linked from our site: www.HighBallSeniorDesign.com/project_documentation.html

It can also be accessed directly here:

https://photos.app.goo.gl/FRyCTfw28V91FpCCA

Appendix E

This appendix contains source code for the GUI application.

The code is located on a public GitHub linked from our site: www.HighBallSeniorDesign.com/project_documentation.html

It can also be accessed directly here:

https://github.com/BrandonRedder/HighBall/tree/master/Software/Ground%20Communication

Appendix F

This appendix contains the source code for the controls simulation.

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

It can also be accessed directly here:

https://github.com/BrandonRedder/HighBall/blob/master/Software/Ground%20Communication/Flight_Simulation.m

Appendix G

This appendix contains FAA regulations pertaining to balloon flight.

The regulations are maintained by Cornell and linked from our site: www.HighBallSeniorDesign.com/project_documentation.html

They can also be accessed directly here:

https://www.law.cornell.edu/cfr/text/14/part-101/subpart-A

Appendix H

This appendix contains FAA regulations pertaining to balloon flight.

The regulations are maintained by Cornell and linked from our site: www.HighBallSeniorDesign.com/project_documentation.html

They can also be accessed directly here:

https://www.law.cornell.edu/cfr/text/14/part-101/subpart-D

Appendix I

This appendix contains a Gantt chart showing the project timeline and major milestones.

The chart is linked from our site: www.HighBallSeniorDesign.com/project_documentation.html

They can also be accessed directly here: www.HighBallSeniorDesign.com/documentation/Gantt.pdf

Appendix J

This appendix contains a PERT chart showing the project timeline and major milestones.

The chart is linked from our site: www.HighBallSeniorDesign.com/project_documentation.html

They can also be accessed directly here: www.HighBallSeniorDesign.com/documentation/PERT.pdf

Appendix K

This appendix contains sensor data from our test flight.

The data is stored on a public GitHub linked from our site: www.HighBallSeniorDesign.com/project_documentation.html

It can also be accessed directly here:

https://github.com/BrandonRedder/HighBall/blob/master/Final%20Documentation/FlightData.xlsx

Appendix L

This appendix contains a final bill of materials for the project.

The BOM is stored on linked from our site: www.HighBallSeniorDesign.com/project_documentation.html

It can also be accessed directly here:

https://drive.google.com/open?id=1pH3nLefY7gUAFXORD74aRVZBpK-clhbAkCagKy8D83Y

High Ball (ECE4012L03) 2

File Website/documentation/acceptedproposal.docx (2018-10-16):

Autonomous Position and Altitude Control System for High Altitude Balloons

ECE4011 Senior Design Project

High Ball

Cohen, Morris

MIT Lincoln Labs

Manning, Mathew W - mathew@gatech.edu

Redder, Brandon A - brandonr@gatech.edu

Richardson, David K - drichardson42@gatech.edu

Sanchez, David - dsanchez36@gatech.edu

Scott, Kristine L - kscott43@gatech.edu

Watters, Kyle - kwatters6@gatech.edu

Submitted

July 20, 2018

Table of Contents

Executive Summary ii

1. Introduction 1
  1.1 Objective 1
  1.2 Motivation 1
  1.3 Background 2
2. Project Description and Goals 2
3. Technical Specification 4
4. Design Approach and Details 5
  4.1 Design Approach 5
    4.1.1 Mechanical Design 5
    4.1.2 Electrical Design 7
    4.1.3 Software Design 9
  4.2 Codes and Standards 10
  4.3 Constraints, Alternatives, and Tradeoffs 11
5. Schedule, Tasks, and Milestones 12
6. Project Demonstration 12
7. Marketing and Cost Analysis 13
  7.1 Marketing Analysis 13
  7.2 Cost Analysis 13
    7.2.1 Hardware Costs 13
    7.2.2 Development Costs 15
8. Current Status 17
9. Leadership Roles 18
10. References 19

Appendix A: Relevant FAA Regulations 22

Appendix B: Project Gantt Chart 29

Appendix C: Project PERT Chart 31

Appendix D: Planned Hardware Purchases 32

Executive Summary

The Georgia Institute of Technology in collaboration with the Massachusetts Institute of Technology Lincoln Laboratory proposes a low-cost autonomous control system for high altitude balloons (HABs). There has been substantial interest in the application of HABs in communication and monitoring of regions not served by traditional infrastructure. Several examples include disaster recovery scenarios, rural areas, and active conflict regions. Many HAB designs suffer from short flight durations, prohibitive cost, or lack position control. The proposed system will employ a low cost altitude and position control system to increase flight duration and regional coverage. The payload will weigh under six pounds to minimize the regulatory burden and allow the balloon to be operated during inclement weather conditions. In order to keep the design under the weight limit and improve structural stability, a novel cutdown mechanism is proposed. To maximize flight duration and regional coverage, an altitude control system will be developed using mechanical methods to release helium and ballast as well as a control algorithm. This algorithm can be combined with measured wind data and weather forecasts to direct the balloon to a specific location. With this extended control, high altitude balloons will be capable of maintaining regional coverage for long periods of time. RF or sensor packages can be deployed using the altitude and position controlled HAB as a stable aerial platform to conduct research, carry out experiments, or conduct surveillance. The expected development cost for the design is $56,649.98 with the cost of hardware per payload being $910.65.

Autonomous Position and Altitude Control System for High Altitude Balloons

1. Introduction

The MITLL High Ball team’s directive is to design, launch, and control a high altitude balloon (HAB). A control system will use varying wind currents at different altitudes to adjust the balloon’s position. The High Ball team is requesting $1000 for development and testing of a viable HAB control system.

  1.1 Objective

The goal of this project is to develop an altitude and location control system for a latex HAB to allow long duration flights over a general location. Algorithms take into account current pressure and temperature conditions when venting helium or dropping ballast to estimate altitude changes. Weather forecasts from the National Oceanic and Atmospheric Administration provide wind speeds at distinct pressure levels allowing for prediction of horizontal movement over time [1]. Using this prediction along with altitude control, the balloon’s position can be controlled.

  1.2 Motivation

High altitude balloons offer a low cost solution for deploying RF and sensor packages. Traditionally, the flight time of an HAB is limited by the balloon bursting. The creation of an altitude control system will drastically improve the flight duration resulting in a larger variety of applications. The proposed control system will allow for prolonged deployment over a specific region.

Project Loon, a balloon system developed by Google, uses tennis court sized balloons to provide cellular service to low population regions. These balloons are capable of multi-month flights with both altitude and location control [2]. Although this system has proven to perform well, it is prohibitively expensive for many applications. A similar position control system deployed on a latex balloon will provide a low cost alternative.

  1.3 Background

As latex HABs rise, the decreasing air pressure causes the balloon to expand until the balloon bursts, ending the flight. Flight times are limited to approximately 3 hours. To overcome this hurdle, balloons have been designed to increase flight durations by venting excess helium upon reaching a predetermined altitude and utilizing polyethylene film which has a lower elasticity than latex to minimize expansion [3]. Zero-pressure balloons must drop ballast to maintain altitude during diurnal cycles, and they can carry loads of up to 6,000 lbs for flights lasting 7-15 days on average [3]. Super pressure balloons rely on a thicker more rigid film material to limit expansion due to changing temperatures, and they can carry loads of up to 2000 lbs for flights lasting over 100 days [3]. For smaller organizations with instrument packages on the scale of 5 lbs these balloon options are unrealistic.

ValBal is a project out of Stanford that produced an altitude control system for latex balloons. The ValBal system holds the current world record for latex balloon flight duration, 121.5 hours [4]. The current design weighs approximately 2.5 kg without ballast and uses a 1500 g balloon with 9 kg of lift allowing the user to include 5 kg of ballast and instruments [4]. Each payload costs $1000 which makes it viable for a much broader range of users [4].

2. Project Description and Goals

The goal is to design a location control system to be used with HABs. The design will utilize altitude change and wind currents to control the location of the balloon. The altitude control system will consist of pressure sensors and an IMU for determining altitude as well as a mechanical release method for ballast and helium. Motion and location of the balloon will be monitored through the use of GPS and an IMU. A microcontroller will be used for data processing and control of mechanical components. The system will be deployed in a single payload so that an additional payload may be attached. The second payload could be used for RF or sensing applications. System features include the following:

- Physical control mechanism for helium and ballast release
- Altitude determination through sensor integration
- Position determination through sensor integration
- Manual control of HAB from ground station
- Autonomous HAB flight
- HAB must be able to reach an altitude of 90,000 ft while maintaining functionality
- Position control using wind currents
- Recoverable payload

3. Technical Specifications

Table 1. Technical Specifications

Feature | Specifications
Operating Voltages | 3.3v, 5v
Battery Capacity | 21000 mAh
Payload Weight | 2500 g
Ballast Weight | 220 g
Operating Altitude | 18 km to 27.4 km
Ambient Operating Temperature | -60℃ to 40℃
Internal Operating Temperature | -35℃ to 40℃
Operating Pressure | 1.0 to 1000.0 hPa
Maximum Recoverable Drop Velocity | 7 m/s
Water Resistance | IPX4
Flight Duration | 24 hours

Table 2. Communications Specifications

Feature | Specifications
Latency | 5 seconds (for message <70 bytes)
Maximum Usable Distance | Global

4. Design Approach and Details

4.1 Design Approach

4.1.1 Mechanical Design

Ballast Release

Ballast will be dispensed via a rotary mechanism from the base of the control payload. The dispenser assembly will consist of 3D printed parts which operate similar to a gumball machine. A 3D rendering of the proposed design is shown in Figure 1. The ballast will be released via a rotating hopper. A set amount of ballast will first move from the chamber to the hopper. This ballast will then be released from the payload. The design prevents a direct connection out of the chamber. The hopper is driven by an aluminum rod connected to a servomotor stored within the electronics bay.


Figure 1. 3D rendering of the proposed ballast dispenser assembly

Helium Venting

Traditional HABs are connected to their payload by a long cord, but to facilitate venting helium from the balloon, a more direct connection is required. This connection is comprised of an adapter attached to the balloon and a bracket mounted to the payload. The adapter has four protruding fins that are locked into place by clamps on the bracket to keep the adapter ending secure. A rubber stopper attached to a spring at the bottom of the bracket plugs the adapter vent preventing helium from escaping during normal operation. This system can be seen in Figure 2. The stopper is attached to a servo located within the payload by a thin rod allowing the servo to adjust the position of the stopper. The rate at which helium leaves the balloon is a function of the size of the opening, atmospheric conditions, and the amount of helium left in the balloon.

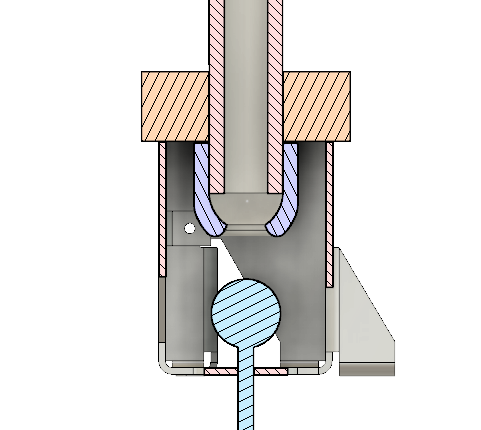
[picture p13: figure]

Figure 2. A mockup of the ball and spring valve used for controlling the release of helium from the balloon.

Cutdown

The balloon will be rigidly connected to the control payload through the helium venting assembly. This connection is held in place with a small section of cord as shown in Figure 3. Nichrome heater wire is threaded within the cord. When the command is given to cutdown the balloon, the controller will energize the nichrome wire by biasing an N-Channel Mosfet driver. This will provide power directly from the battery to the nichrome wire, bypassing the voltage regulation circuitry. To control current, the driver is connected to a pulse width modulation pin on the controller.

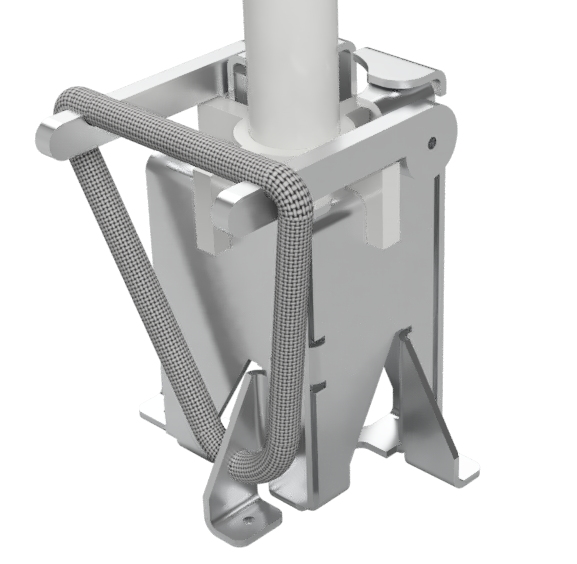
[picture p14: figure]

Figure 3. A 3D model balloon cutdown mechanism and its connection to the helium venting assembly

    4.1.2 Electrical Design

Communication

Communications between the balloon and the ground station are facilitated through the Iridium satellite network by an Iridium short burst data transceiver. To conserve data, information sent over satellite is not stored in traditional data types. Taking advantage of the minimum and maximum values expected for each data field (the altitude will be between -5000 and 35000 meters) and the precision of current hardware (altitude will be accurate to within 3 meters), it is possible to store the data using the smallest number of bits without decreasing the precision.

Microcontroller

The microcontroller will be an Arduino Mega 2560 development board (based on the ATmega2560). It was selected due to its ease of use, low cost, and communication capabilities. The controller is connected to the other sensors with headers attached to a custom PCB.

Sensors

Several sensors will be used to provide data to the controller. Each of the sensors are summarized below:

- GPS Module
  - The GPS module is the primary method of monitoring the position of the balloon. It was specially chosen due to its “balloon mode” which allows it to continue functioning beyond 65,000 feet.
- Altimeters (2x)
  - The altimeters provide critical altitude information which is used to control helium and ballast releases. They are included as a pair to mitigate the potential of sensor failure.
- Inertial Measurement Unit
  - The inertial measurement unit (IMU) will be used to provide an estimation of the payloads orientation and position. This data will also be used for fall detection should the balloon burst or unintentionally separate from the payload.
- Analog Temperature Sensor
  - The temperature sensor will be used to monitor payload temperature and control the payload heater as needed. For the first flight, it will be configured to operate the heater with proportional integral derivative (PID) control.

4.1.3 Software

Ground Station Interface

The ground station interface will consist of a GUI displaying the current condition of the HAB and options to change the altitude. The location of the HAB will be displayed as well as the direction of movement. The GUI will also show live wind data at different altitudes. The user will have an option to manually control the altitude of the balloon as well as cutdown.

Altitude Control

Changing altitude will be the main method of directing the HAB to stay within a set radius by following wind currents. To do this, both wind data and altitude measurements are required. To determine altitude, altimeter and IMU data will be fused [5]. Having the inertial data from the IMU will also give insight into when to stop releasing ballast or venting helium so that the balloon will stop ascending/descending at the correct altitude.

Temperature Control

The temperature of the payload will be regulated with a small heating element. This heater will be controlled with a PID algorithm that using measurements from the analog temperature sensor.

Wind Detection

The effects of wind will be seen in the movement of the HAB. In order to reliably and precisely determine change in position, GPS and IMU data will be fused. GPS location outputs can be unreliable in certain locations and the selected GPS has a position resolution of 3 m. Fusing the data from the GPS with inertial data from the IMU will provide more accurate information than if either method is used alone. The fused data will be used to calculate horizontal movement which correlates with wind currents.

  4.1 Codes and Standards

FAA Title 14 - Part 101 - Subpart A (Appendix A) describes the conditions under which unmanned civilian vehicles may be operated within the United States. Part 101.1 specifies that any unmanned free balloon must comply with subpart D with the exception of balloons that:

- Carries a payload package that weighs more than four pounds and has a weight/size ratio of more than three ounces per square inch on any surface of the package, determined by dividing the total weight in ounces of the payload package by the area in square inches of its smallest surface
- Carries a payload package that weighs more than six pounds
- Carries a payload of two or more packages that weighs more than 12 pounds
- Uses a rope or other device for suspension of the payload that requires an impact force of more than 50 pounds to separate the suspended payload from the balloon

The regulations in Subpart D (Appendix A) directly interfere with the intended application of the system, so the payload is designed to comply with the exceptions listed in Part 101.1.

Part 101.7, as it applies to unmanned free balloons, prohibits the operation of the balloon in a manner that may be hazardous to other persons, or their property. It also prohibits dropping any objects, if such an action creates a hazard [6].

FCC Title 47 - Part 97.113 lists prohibited transmissions on amateur radio wavelengths. Relating to this project, no station shall transmit communications for hire or for material compensation, direct or indirect, paid or promised, except as otherwise provided in these rules [7]. This regulation makes amatueur radio an unsuitable means of communication for the system due to the commercial nature of the project.

FCC Title 47 - Part 22.925 prohibits the use of cellular phones while airborne, preventing the system from using a cellular phone to communicate with the payload during flight [8].

The Iridium 9603 transceiver utilized in this design has been granted authorization by the FCC as a Licensed Non-Broadcast Station Transmitter under the conditions listed in FCC Title 47 - Part 25 [9]. The grant of equipment authorization requires that the transmitter be installed to provide 20 cm of separation distance from all persons, and must not be operation in conjunction with any other transmitter within a host device [10].

  4.2 Constraints, Alternatives, and Tradeoffs

Due to FAA regulations, the payload weight must be less than 6 lb [6]. This restriction results in a tradeoff between component selection and ballast weight. Maximizing the amount of ballast is important for increasing flight duration, but longer flights require a larger power supply. Further testing will allow optimization of this tradeoff.

Due to the altitude of HAB flights, the system must be able to sustain operations in temperatures as low as -60° C. Many electronic components fail at this temperature, so special considerations must be made to insulate the payload. An insulated enclosure will protect the electronics from cold temperatures. Additionally, a heater will be installed during the initial test flight to insure correct operation.

4 Schedule, Tasks, and Milestones

The expected GANTT and PERT chart are shown below in Appendix B and C respectively.

5 Project Demonstration

Demonstration

The project demonstration will consist of an HAB launch followed by monitoring from the ground station. Validation of the project specifications will be based on data gathered from the ground station and the payload. Retaining control of the altitude during the demonstration will validate the altitude control system. Navigating the balloon to a region and maintaining position within that region will validate the position control system. Validation of both the altitude and position control systems constitutes a successful demonstration.

Testing

Replicating the conditions of the stratosphere on the ground will not be feasible for this project, so ground testing will not be enough to validate the overall system feasibility. Instead, the predicted conditions will be simulated to test the control algorithm. The ballast release and cutdown mechanisms can be tested at ground level by performing the tests in a freezer. Initial tests for the helium release mechanism will be performed on the ground; however, they will not be able to fully account for the actual conditions. Ground tests will be used to test position and altitude determination algorithms, but they will not allow for sufficient hardware testing. Battery life can be calculated by measuring power draw from each electrical component. This will provide an estimate for maximum flight duration.

6 Marketing and Cost Analysis
  6.1 Marketing Analysis

It is not plausible to launch a HAB project at the same scale as Project Loon unless adequate funding is acquired [2]. Stanford University's ValBal team developed a low cost alternative. The ValBal project utilized less than $1,000 to achieve the longest recorded latex balloon flight. The Stanford team’s aircraft used an altitude control system to extend the flight duration [11]. In addition to altitude control, the proposed design aims to develop a position control system. Position control is a novel concept in the domain of inexpensive HABs.

The ValBal design exceeds the weight limit specification which requires users to follow FAA regulations 101.33, 101.35, 101.37, and 101.39 [6] [11]. The proposed design will weigh less than six pounds which will allow for an additional six pound payload without needing to follow the above FAA regulations. Of particular importance, the proposed system may be operated during inclement weather conditions without prior notice to the FAA [6].

  6.2 Cost Analysis

7.2.1 Hardware Costs

The HAB control system will consist of electronic, mechanical, and structural components. The previous design effort purchased some supplies that can be reused shown in Table 3. These items are not included in the final cost calculations.

Table 3. Previous Supplies

Item | Estimated Cost
Arduino Mega 2560 | $38.50
5 ft Diameter Parachute | $50
1200 g Latex Balloon | $120
RockBLOCK Iridium Module | $250
Servos | $80

The additional parts necessary to build the proposed design are listed in Appendix D. The listed components provide enough materials for a single launch. Further launches will require additional balloons and potentially hardware if the payload is not recovered.

In addition to hardware, the satellite communication in use will require a data plan with monthly costs and additional charges for data usage, checking for messages, and registering the device as shown in Table 4.

Table 4. Communication Data Plan Charges

Monthly Subscription Fee | $14.99
Data Charge | $1.09 / KB
Minimum Billing Increment per Message | 30 bytes
Cost of 30 Byte Message | $0.03
Mailbox Check | $0.05
Registration Fee | $0.05

Table 5 estimates the total cost communication for each predicted flight. These costs are calculated based on 20 messages and 12 mailbox checks per hour. The total estimated cost for the communication plan over 3 months is $112.69.

Table 5. Balloon Communication Costs

Flight Number | Duration (hrs) | Monthly Cost | Message Cost | Mailbox Cost | Total
1 | 6 | $14.99 | $3.92 | $3.60 | $22.51
2 | 24 | $14.99 | $15.70 | $14.4 | $45.09
3 | 24 | $14.99 | $15.70 | $14.4 | $45.09
Total Cost | | | | | $112.69

7.2.2 Development Costs

The design team will consist of six engineers. Table 6 shows the number of work hours per engineer estimated for the duration of the project.

Table 6. Number of Work Hours per Engineer

Task | Hours
Sensor Integration | 8
Algorithm Development and Implementation | 20
Research | 5
Meetings | 15
Parts Fabrication | 10
Assembly | 10
Ground Testing | 5
Launches and Launch Preparation | 15
Presentation | 2
Reports | 12
Total | 102

Each engineer is estimated to have a salary of $65,000, per year [12]. The United States Office of Personnel Management defines one work year as 2087 hours [13]. Using these estimates, the hourly rate of a single engineer is $31.15. A fringe benefit rate of 31.9% and an overhead rate of 120% are assumed [14]. The total development costs under these assumptions are shown in Table 7.

Table 7. Total Project Costs

Project Section | Cost
Parts | $492.15
Communication Costs | $112.69
Labor | $19,063.80
Fringe Benefits (31.9% of Labor) | $6081.35
Subtotal | $25,749.99
Overhead (120% of Subtotal) | $30,899.99
Total | $56,649.98

7 Current Status

The previous design team took significant steps towards implementing a functional altitude control system. Unfortunately, many of the components are not rated at the altitudes and temperatures experienced during a HAB flight. The proposed design overhauls the existing hardware and large sections of the code to account for the replacement hardware. At this time, a bill of materials has been created and is in the process of being ordered. In the immediate future, the team will begin work on developing a functional altitude control system for the new hardware and will prepare for a launch late August.

9 Leadership Roles

Mathew’s leadership duties include ensuring the team follows proper operating protocol to better ensure safety and is the embedded systems lead. Brandon’s leadership duties include acting as the main correspondent and webmaster as well as leading hardware assembly. David R.’s leadership duties include being the software lead in addition to ensuring documentation is complete and all writing guidelines and deadlines are met. David S.’s leadership role includes procuring and managing transportation in addition to being the communication systems lead. Kristine’s leadership duties include coordinating the final expo as well as leading sensor integration and GUI development. Kyle’s leadership positions include launch preparation and control systems lead.

11 References

[1] National Oceanic and Atmospheric Administration, “Global Forecast System (GFS),” July 14, 2018. [Online]. Available: https://www.ncdc.noaa.gov/data-access/model-data/model-datasets/global-forcast-system-gfs
[Accessed: July 20, 2018].

[2] X Development LLC, “Technology,” Project Loon, 2018, [Online]. Available: https://loon.co/technology/ [Accessed: Jun. 8, 2018].

[3] B. Dunbar, H. Zell, “Types of Balloons”, National Aeronautics and Space Administration, Aug. 3, 2017 [Online]. Available: https://www.nasa.gov/scientific-balloons/types-of-balloons [Accessed July 19, 2018].

[4] Andrey Sushko, Aria Tedjarati, Joan Creus-Costa, Kai Marshland, Paige Brown, Davy Ragland, John Dean, Sasha Maldonado, John M. Pauly, “Advancements in low-cost, long endurance, altitude controlled latex balloons (ValBal),” In Proc. 2018 IEEE Aerospace Conference, 2017 pp. 1-9. [Online]. Available: https://ieeexplore.ieee.org/document/8396588/ [Accessed: July 20, 2018].

[5] Y. Son and S. Oh, "A barometer-IMU fusion method for vertical velocity and height estimation," 2015 IEEE SENSORS, Busan, 2015, pp. 1-4. [Online]. Available: https://ieeexplore.ieee.org/stamp/stamp.jsp?tp=&arnumber=7370269 [Accessed: July 19, 2018].

[6] Code of Federal Regulations Title 14 Part 101 (14CFR101), Moored Balloons, Kites, Amateur Rockets, Unmanned Free Balloons, and Certain Model Aircraft [Online]. Available: https://ecfr.io/Title-14/pt14.2.101#sp14.2.101 [Accessed: July 19, 2018].

[7] Code of Federal Regulations Title 47 Part 97.113, Amateur Radio Service, Prohibited Transmissions [Online]. Available: https://ecfr.io/Title-47/se47.5.97_1113 [Accessed: July 19, 2018].

[8] Code of Federal Regulations Title 47 Part 22.925, Public Mobile Services, Prohibition on Airborne Operation of Cellular Telephones [Online]. Available: https://ecfr.io/Title-47/pt47.2.22#se47.2.22_1925 [Accessed: July 19, 2018].

[9] Code of Federal Regulations Title 47 Part 25, Satellite Communications [Online]. Available: https://ecfr.io/Title-47/pt47.2.25 [Accessed: July 19, 2018].

[10] Iridium Communications Inc, “Iridium 9603 Short Burst Data Modem: Declaration of Conformity,” Iridium Short Burst Data (SBD), July 19, 2018. [Online]. Available: https://www.iridium.com/file/24245/ [Accessed: July 20, 2018].

[11] A. Sushko, A. Tedjarati, J. Crues-Costa, S. Maldonado, K. Marshland, and M. Pavone, “Low Cost, High Endurance, Altitude-Controlled Latex Balloon for Near-Space Research (ValBal),” In Proc. IEEE Aerospace Conference ’03, 2017, pp. 1-9. [Online]. Available: http://ieeexplore.ieee.org/stamp/stamp.jsp?tp=&arnumber=7943912&isnumber=7943554 [Accessed: July 20, 2018].

[12] Georgia Tech School of Electrical and Computer Engineering, “What is ECE at Georgia Tech,” Georgia Institute of Technology, 2018. para. 11, Apr. 4, 2018 [Online]. Available: https://www.ece.gatech.edu/what-ece-georgia-tech [Accessed July 19, 2018].

[13] US Office of Personnel Management, “ Pay & Leave: Pay Administration,” OPM.gov, para. 1. [Online]. Available: https://www.opm.gov/policy-data-oversight/pay-leave/pay-administration/fact-sheets/computing-hourly-rates-of-pay-using-the-2087-hour-divisor/ [Accessed: July 19, 2018].

[14] Georgia Tech Office of Sponsored Programs, “Facilities & Administrative Rates,” Georgia Tech Office of Sponsored Programs, para. 3, July 6, 2018. [Online]. Available: http://www.osp.gatech.edu/rates [Accessed: July 19, 2018].

Appendix A: Relevant FAA Regulations

Subpart A—General

§101.1 Applicability.

(a) This part prescribes rules governing the operation in the United States, of the following:

(1) Except as provided for in §101.7, any balloon that is moored to the surface of the earth or an object thereon and that has a diameter of more than 6 feet or a gas capacity of more than 115 cubic feet.

(2) Except as provided for in §101.7, any kite that weighs more than 5 pounds and is intended to be flown at the end of a rope or cable.

(3) Any amateur rocket except aerial firework displays.

(4) Except as provided for in §101.7, any unmanned free balloon that—

(i) Carries a payload package that weighs more than four pounds and has a weight/size ratio of more than three ounces per square inch on any surface of the package, determined by dividing the total weight in ounces of the payload package by the area in square inches of its smallest surface;

(ii) Carries a payload package that weighs more than six pounds;

(iii) Carries a payload, of two or more packages, that weighs more than 12 pounds; or

(iv) Uses a rope or other device for suspension of the payload that requires an impact force of more than 50 pounds to separate the suspended payload from the balloon.

(5) Any model aircraft that meets the conditions specified in §101.41. For purposes of this part, a model aircraft is an unmanned aircraft that is:

(i) Capable of sustained flight in the atmosphere;

(ii) Flown within visual line of sight of the person operating the aircraft; and

(iii) Flown for hobby or recreational purposes.

(b) For the purposes of this part, a gyroglider attached to a vehicle on the surface of the earth is considered to be a kite.

[Doc. No. 1580, 28 FR 6721, June 29, 1963, as amended by Amdt. 101-1, 29 FR 46, Jan. 3, 1964; Amdt. 101-3, 35 FR 8213, May 26, 1970; Amdt. 101-8, 73 FR 73781, Dec. 4, 2008; 74 FR 38092, July 31, 2009; Docket FAA-2015-0150, Amdt. 101-9, 81 FR 42208, June 28, 2016]

§101.3 Waivers.

No person may conduct operations that require a deviation from this part except under a certificate of waiver issued by the Administrator.
[Doc. No. 1580, 28 FR 6721, June 29, 1963]

§101.5 Operations in prohibited or restricted areas.

No person may operate a moored balloon, kite, amateur rocket, or unmanned free balloon in a prohibited or restricted area unless he has permission from the using or controlling agency, as appropriate.
[Doc. No. 1457, 29 FR 46, Jan. 3, 1964, as amended at 74 FR 38092, July 31, 2009]

§101.7 Hazardous operations.

(a) No person may operate any moored balloon, kite, amateur rocket, or unmanned free balloon in a manner that creates a hazard to other persons, or their property.
(b) No person operating any moored balloon, kite, amateur rocket, or unmanned free balloon may allow an object to be dropped therefrom, if such action creates a hazard to other persons or their property.
(Sec. 6(c), Department of Transportation Act (49 U.S.C. 1655(c)))
[Doc. No. 12800, 39 FR 22252, June 21, 1974, as amended at 74 FR 38092, July 31, 2009]

Subpart D—Unmanned Free Balloons
Source: Docket No. 1457, 29 FR 47, Jan. 3, 1964, unless otherwise noted.

§ 101.31 Applicability.
This subpart applies to the operation of unmanned free balloons. However, a person operating an unmanned free balloon within a restricted area must comply only with § 101.33 (d) and (e) and with any additional limitations that are imposed by the using or controlling agency, as appropriate.

§ 101.33 Operating limitations.
No person may operate an unmanned free balloon—

(a) Unless otherwise authorized by ATC, below 2,000 feet above the surface within the lateral boundaries of the surface areas of Class B, Class C, Class D, or Class E airspace designated for an airport;
(b) At any altitude where there are clouds or obscuring phenomena of more than five-tenths coverage;
(c) At any altitude below 60,000 feet standard pressure altitude where the horizontal visibility is less than five miles;
(d) During the first 1,000 feet of ascent, over a congested area of a city, town, or settlement or an open-air assembly of persons not associated with the operation; or
(e) In such a manner that impact of the balloon, or part thereof including its payload, with the surface creates a hazard to persons or property not associated with the operation.

[Doc. No. 1457, 29 FR 47, Jan. 3, 1964, as amended by Amdt. 101-5, 56 FR 65662, Dec. 17, 1991]

§ 101.35 Equipment and marking requirements.
(a) No person may operate an unmanned free balloon unless—

(1) It is equipped with at least two payload cut-down systems or devices that operate independently of each other;

(2) At least two methods, systems, devices, or combinations thereof, that function independently of each other, are employed for terminating the flight of the balloon envelope; and

(3) The balloon envelope is equipped with a radar reflective device(s) or material that will present an echo to surface radar operating in the 200 MHz to 2700 MHz frequency range. The operator shall activate the appropriate devices required by paragraphs

(a) (1) and (2) of this section when weather conditions are less than those prescribed for operation under this subpart, or if a malfunction or any other reason makes the further operation hazardous to other air traffic or to persons and property on the surface.

(b) No person may operate an unmanned free balloon below 60,000 feet standard pressure altitude between sunset and sunrise (as corrected to the altitude of operation) unless the balloon and its attachments and payload, whether or not they become separated during the operation, are equipped with lights that are visible for at least 5 miles and have a flash frequency of at least 40, and not more than 100, cycles per minute.
(c) No person may operate an unmanned free balloon that is equipped with a trailing antenna that requires an impact force of more than 50 pounds to break it at any point, unless the antenna has colored pennants or streamers that are attached at not more than 50 foot intervals and that are visible for at least one mile.

(d) No person may operate between sunrise and sunset an unmanned free balloon that is equipped with a suspension device (other than a highly conspicuously colored open parachute) more than 50 feet along, unless the suspension device is colored in alternate bands of high conspicuity colors or has colored pennants or streamers attached which are visible for at least one mile.

(Sec. 6(c), Department of Transportation Act (49 U.S.C. 1655(c)))
[Doc. No. 1457, 29 FR 47, Jan. 3, 1964, as amended by Amdt. 101-2, 32 FR 5254, Mar. 29, 1967; Amdt. 101-4, 39 FR 22252, June 21, 1974]

§ 101.37 Notice requirements.

(a) Prelaunch notice: Except as provided in paragraph (b) of this section, no person may operate an unmanned free balloon unless, within 6 to 24 hours before beginning the operation, he gives the following information to the FAA ATC facility that is nearest to the place of intended operation:

(1) The balloon identification.

(2) The estimated date and time of launching, amended as necessary to remain within plus or minus 30 minutes.

(3) The location of the launching site.

(4) The cruising altitude.

(5) The forecast trajectory and estimated time to cruising altitude or 60,000 feet standard pressure altitude, whichever is lower.

(6) The length and diameter of the balloon, length of the suspension device, weight of the payload, and length of the trailing antenna.

(7) The duration of flight.

(8) The forecast time and location of impact with the surface of the earth.

(b) For solar or cosmic disturbance investigations involving a critical time element, the information in paragraph (a) of this section shall be given within 30 minutes to 24 hours before beginning the operation.

(c) Cancellation notice: If the operation is canceled, the person who intended to conduct the operation shall immediately notify the nearest FAA ATC facility.

(d) Launch notice: Each person operating an unmanned free balloon shall notify the nearest FAA or military ATC facility of the launch time immediately after the balloon is launched.

§ 101.39 Balloon position reports.

(a) Each person operating an unmanned free balloon shall:

(1) Unless ATC requires otherwise, monitor the course of the balloon and record its position at least every two hours; and

(2) Forward any balloon position reports requested by ATC.

(b) One hour before beginning descent, each person operating an unmanned free balloon shall forward to the nearest FAA ATC facility the following information regarding the balloon:

(1) The current geographical position.

(2) The altitude.

(3) The forecast time of penetration of 60,000 feet standard pressure altitude (if applicable).

(4) The forecast trajectory for the balance of the flight.

(5) The forecast time and location of impact with the surface of the earth.

(c) If a balloon position report is not recorded for any two-hour period of flight, the person operating an unmanned free balloon shall immediately notify the nearest FAA ATC facility. The notice shall include the last recorded position and any revision of the forecast trajectory. The nearest FAA ATC facility shall be notified immediately when tracking of the balloon is re-established.

(d) Each person operating an unmanned free balloon shall notify the nearest FAA ATC facility when the operation is ended.

Appendix B: Project Gantt Chart

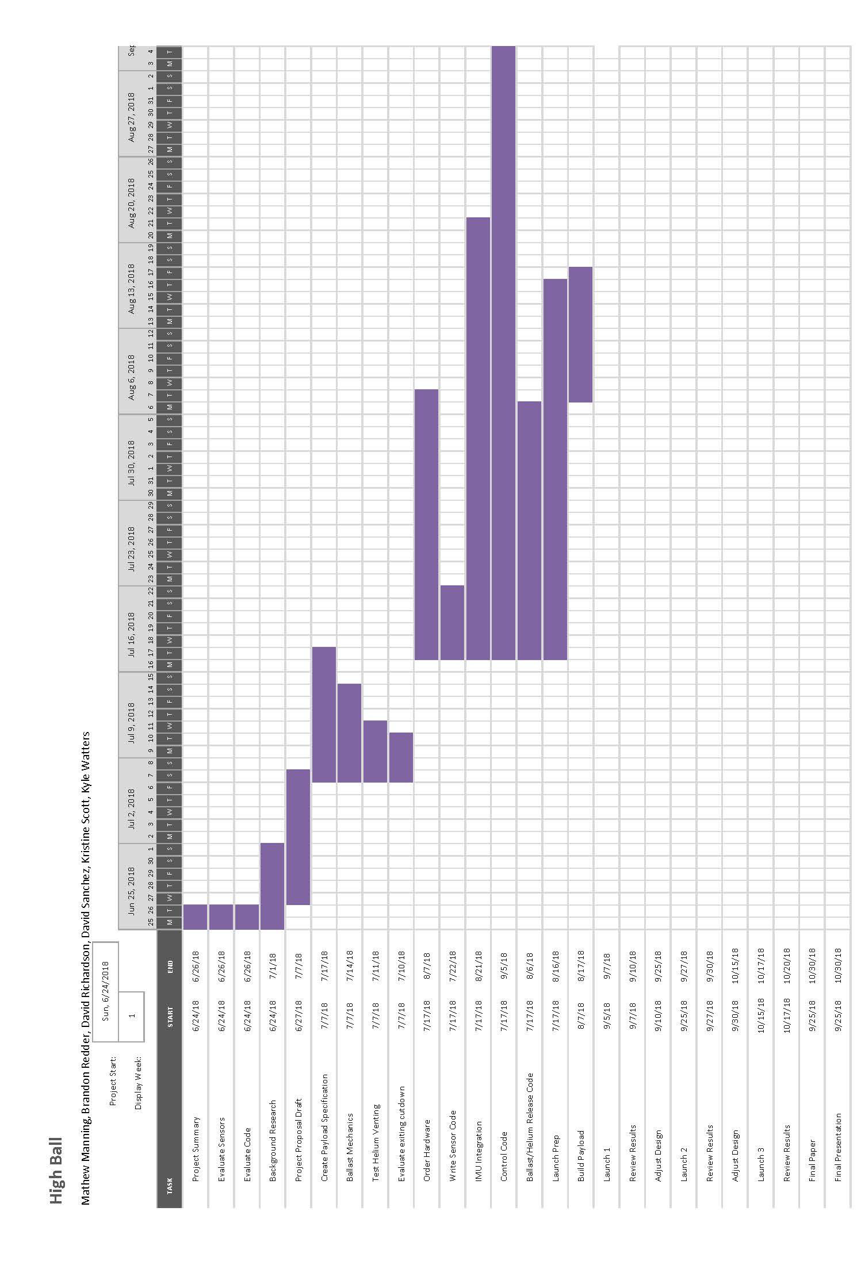
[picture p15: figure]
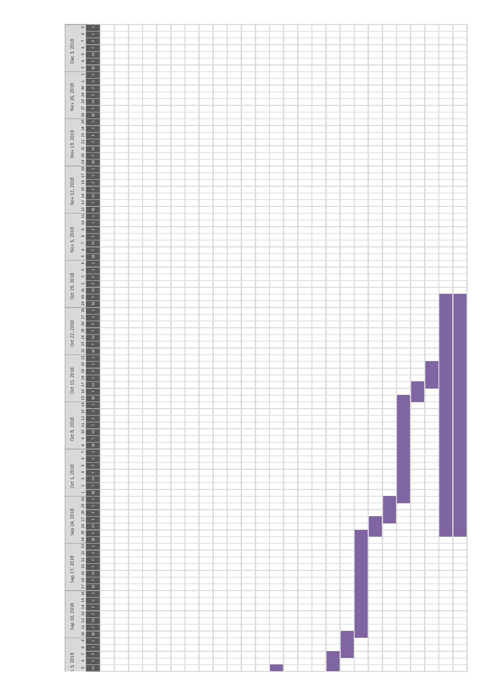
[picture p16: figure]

Appendix C - PERT Chart

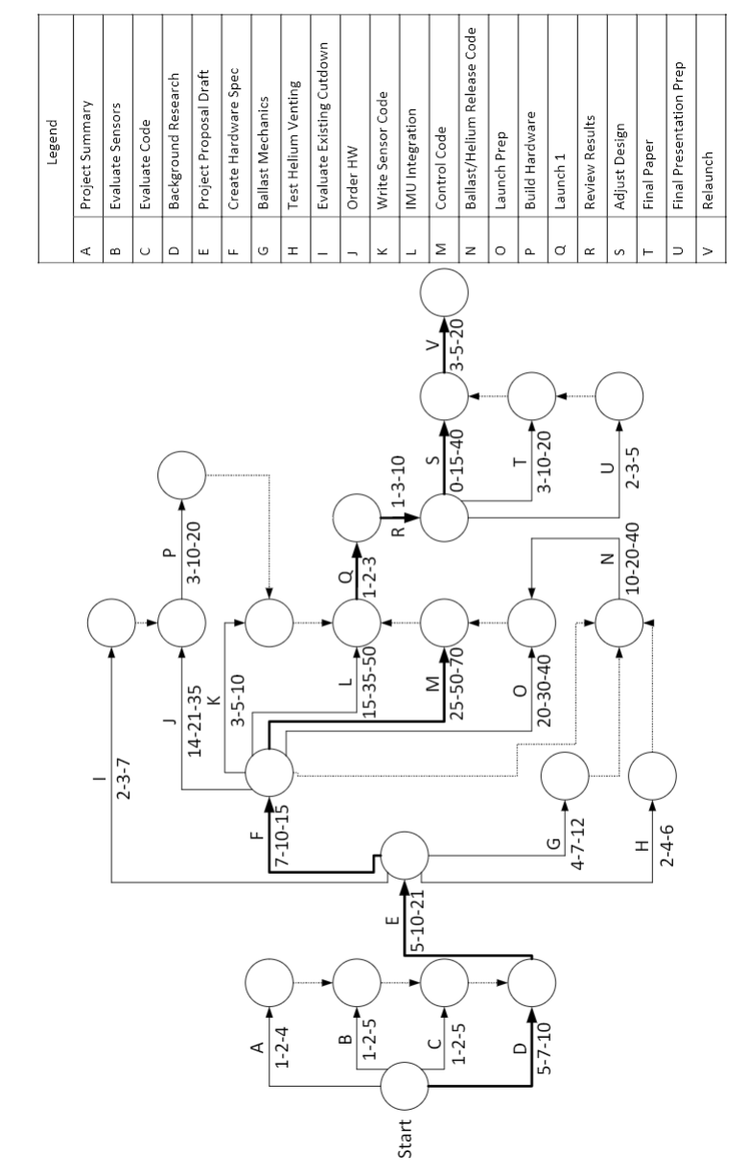
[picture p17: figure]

Appendix D: Planned Hardware Purchases

Name | Vendor | SKU | Quantity | Unit Cost | Subtotal
Nichrome Wire | Amazon | - | 1 | $6.49 | $6.49
SENSOR TEMP ANLG VOLT TO-92-3 | Digikey | LM335ZNS/NOPB-ND | 1 | $1.32 | $1.32
1200g Balloon | High Altitude Science | - | 1 | $120.00 | $120.00
.75" to .5" PVC Reducer | Home Depot | PVC 02100 3400HD | 2 | $0.58 | $1.16
.5" PVC Pipe | Home Depot | 22015 | 2 | $1.26 | $2.52
.5" PVC Cap | Home Depot | C447-005 | 2 | $0.49 | $0.98
FOAMULAR 150 1 in. x 4 ft. x 8 ft. R-5 Scored Square Edge Rigid Foam Board Insulation Sheathing | Home Depot | - | 2 | $18.98 | $37.96
1/4" Aluminum Round Bar (24" long) | Metal Supermarkets | AR6061/14 | 1 | $13.33 | $13.33
0.08" Aluminum Sheet (8.5" x 8.5") | Metal Supermarkets | ASH6061/080 | 1 | $21.42 | $21.42
Iridium SBD Plan | Satphone Store | 13-SBD-BASIC | 1 | $14.99 | $14.99
SparkFun Pressure Sensor Breakout - MS5803-14BA | Sparkfun | SEN-12909 | 2 | $59.95 | $119.90
3D Download: STL, IGES, STEP Servo Shaft Coupler - Hitec Standard | Sparkfun | ROB-12501 | 2 | $4.99 | $9.98
SparkFun GPS Breakout - XA1110 (Qwiic) | Sparkfun | SEN-12909 | 1 | $59.95 | $59.95
Screw Terminal | Sparkfun | PRT-10571 | 1 | $0.75 | $0.75
9DoF Razor IMU M0 | Sparkfun | SEN-14001 | 1 | $34.95 | $34.95
SparkFun Logic Level Converter - Bi-Directional | Sparkfun | BOB-12009 | 1 | $2.95 | $2.95
Heating Pad - 5x10cm | Sparkfun | COM-11288 | 1 | $3.95 | $3.95
3/8" Plastic Standoff | Sparkfun | PRT-10461 | 2 | $2.95 | $5.90
#4-40 Machine Screw | Sparkfun | PRT-10453 | 2 | $1.50 | $3.00

N-Channel Mosfet | Sparkfun | COM-10213 | 2 | $0.95 | $1.90
Servo Cable | Sparkfun | ROB-08738 | 2 | $2.95 | $5.90
RockBLOCK 9603 Accessory Cable | Sparkfun | CAB-14720 | 1 | $4.95 | $4.95
Interface Cable SMA to U.FL | Sparkfun | WRL-09145 | 1 | $4.95 | $4.95
Antenna GPS 3V Magnetic Mount SMA | Sparkfun | GPS-00464 | 1 | $12.95 | $12.95
Total Hardware Purchases | | | | | $492.15

High Ball 2

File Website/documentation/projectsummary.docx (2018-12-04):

ECE 4011/ECE 4012 Project Summary

Project Title | MITLL High Ball
Team Members (names and majors) | Mathew Manning (CmpE)
| Brandon Redder (EE)
| David Richardson (EE)
| David Sanchez (EE)
| Kristine Scott (EE)
| Kyle Watters (EE)
Advisor / Section | Morris Cohen, Witt Smith – A05
Semester | Summer 2018 – ECE 4011

Project Abstract
(250-300 words)

High Altitude Balloons (HABs) are primarily used for capturing aerial imagery, observing atmospheric conditions, and conducting test in near-space conditions. HABs are a low cost alternative to other high altitude vehicles such as drones, HABs with payloads under six pounds are lightly regulated in the United States, and operating an HAB requires less training than other unmanned aircraft suitable for aerial surveillance. The largest drawbacks to latex HABs are the limited flight times and lack of control over flight path. Normally during ascension the gas filling the balloon expands as atmospheric pressure drops causing the balloon to burst and ending the flight. The balloon’s path is reliant on wind currents, and the flight time is limited by rate of ascension and the burst altitude of the system. Teams across the country have designed altitude control systems for HABs that alternatively release gas or ballast from the system to keep the balloon within operating altitudes, increasing flight duration. This project developed a method of controlling altitude with future goals of implementing a position control system. Future work will utilize wind speed and direction variation with altitude to allow the balloon to navigate to a specified location.

The importance of directing the course of the HAB is tied to the intended use of the system. The project focused on designing an HAB system which will capture aerial images during and after natural disasters to help disaster relief teams track evolving situations. Current high altitude balloons are impractical for this purpose because they cannot remain over the target area for long enough, and high altitude planes or drones are cost prohibitive. The project has the potential to improve the effectiveness of disaster relief teams when they are needed most.

Project Title | MITLL High Ball

List codes and standards that significantly affect your project. Briefly describe how they influenced your design.

Federal Codes (FAA Regulations)

(Title 14 CFR 101.1) General Applicability

This part prescribes rules governing the operation in the United States, of the following:

4) Except as provided for in § 101.7, any unmanned free balloon that -

(i) Carries a payload package that weighs more than four pounds and has a weight/size ratio of more than three ounces per square inch on any surface of the package, determined by dividing the total weight in ounces of the payload package by the area in square inches of its smallest surface;
(ii) Carries a payload package that weighs more than six pounds;
(iii) Carries a payload, of two or more packages, that weighs more than 12 pounds; or
(iv) Uses a rope or other device for suspension of the payload that requires an impact force of more than 50 pounds to separate the suspended payload from the balloon.

(Title 14 CFR 101.33) Operating Limitations

The balloon may not operate within: Class B, C, D, or E airspace, below 2,000 feet, clouds below 60,000 feet, above a populated area while below 1,000 feet, or in any manner which may cause hard to person(s) or property below.

(Title 14 CFR 101.35) Equipment and Marking Requirements

The balloon must be equipped with two independent cutdown systems, radar reflective devices (or surfaces which echo radar operating in the 200 MHz. to 2700 MHz. frequency range). The balloon must be cutdown should conditions drop below minimums specified in 14 CFR 101.33. The balloon must be equipped with lights which are visible for at least 5 miles and have a flashing frequency between (40 and 100 cycles per minute) to operate below 60,000 feet between sunset and sunrise.

(Title 14 CFR 101.37) Notice Requirements

Between 6 and 24 hours before launch, the balloon’s operator must notify FAA ATC of balloon identification, estimated date/time of launch (+/- 30 minutes accuracy), location of launch site, cruising altitude, forecast trajectory, estimated time to cruising altitude, length and diameter of balloon, length of suspension device, weight of payload, duration of flight, forecast time and location of impact with surface of earth. FAA ATC must be notified of cancelation. FAA ATC must be notified immediately after launch.

(Title 14 CFR 101.39) Balloon Position Reports

The course of the balloon must be monitored with each position being recorded (at minimum) every 2 hours. Balloon position reports must forward to FAA ATC at request. One (1) hour before beginning descent the operator must notify FAA ATC of current geographic position, altitude, forecast time of penetration of 60,000 feet, forecast trajectory for balance of flight, forecast time and location of impact with surface of earth. If a balloon position report is not recorded for any 2 hour time period, the operator shall immediately notify FAA ATC with the last recorded position and any revisions to the forecast trajectory. Upon re-establishment of tracking FAA ATC shall be notified.

FCC Regulations for Cell Phone and Amatuer Radio Communications

(Title 47 CFR 22.925) Prohibition on airborne operation of cellular telephones.
Cellular telephones installed in or carried aboard airplanes, balloons or any other type of aircraft must not be operated while such aircraft are airborne (not touching the ground). When any aircraft leaves the ground, all cellular telephones on board that aircraft must be turned off. The following notice must be posted on or near each cellular telephone installed in any aircraft:

“The use of cellular telephones while this aircraft is airborne is prohibited by FCC rules, and the violation of this rule could result in suspension of service and/or a fine. The use of cellular telephones while this aircraft is on the ground is subject to FAA regulations.”

(Title 47 CFR 97.113) Prohibited transmissions

(a) No amateur station shall transmit

(2) Communications for hire or for material compensation, direct or
indirect, paid or promised, except as otherwise provided in these rules;
Page 4
(3) Communications in which the station licensee or control operator
has a pecuniary interest, including communications on behalf of an
employer.
(5) Communications, on a regular basis, which could reasonably be
furnished alternatively through other radio services

Design Implications

FAA regulations constrained the weight and weight per square inch of the design, and FCC regulations limited the form of communication. Assuming the altitude control system is functional and no hardware problems occur, a flight will be terminated when the battery dies or all of the ballast is used. The regulations relating to weight limit the size of the battery and the amount of ballast that can be used, which limit the maximum flight time. Our system will prioritize ballast over battery weight since the position control will use ballast more often than pure altitude control systems. The limits on the weight per square inch affect the shape of the system, eliminating any structure with a thin profile, increasing the internal volume. The larger volume is harder to heat, so our design will section off areas of the frame containing components sensitive to temperature, humidity, and shock. Communication between the balloon and the ground station is already limited by the distance and possible interference in the atmosphere, so regulations against cellular channels at high altitudes and amateur radio for commercial uses lead the team to utilizing satellite communications.

List at least two significant realistic design constraints that applied to your project. Briefly describe how they affected your design.

1. The payload must weigh less than 6 lbs. This has to be considered when choosing the materials for the structure, and the hardware used in the payload. The weight of the ballast and battery will directly limit the maximum flight duration.
2. Battery must last for the duration of the flight. The size of the battery and the power consumption of the electronics must be taken into consideration because the weight of the battery must be as small as possible.
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

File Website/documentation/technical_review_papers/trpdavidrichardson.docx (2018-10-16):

Altitude Measurement for Weather Balloon Altitude Control

Introduction

Altitude measurement has played an important part in aviation since the development of the first accurate altimeter in 1928 [1]. Other aerial vehicles have begun using altimeters for elevation control. Recent research suggests similar altitude control systems can be implemented into high altitude balloons [2]. High altitude balloons require small, lightweight measurement instruments, so altimeters are typically used. Typically, small measurement devices are less accurate than large designs, but altimeters can maintain accuracy by using microelectromechanical systems (MEMS). Additional methods of measuring altitude include GPS and laser altimetry. This paper reviews some commercially available altitude measurement devices and explains different altitude measurement techniques as well as how these devices are implemented.

Techniques for Altitude Measurement

Pressure Altimeter
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

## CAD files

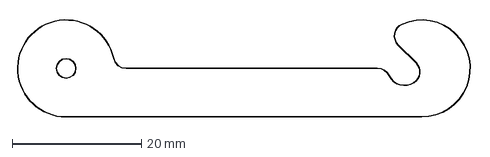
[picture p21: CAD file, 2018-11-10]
Hardware/CAD Parts/Hold_Down_Arms.dxf
70.9 x 15.6 mm

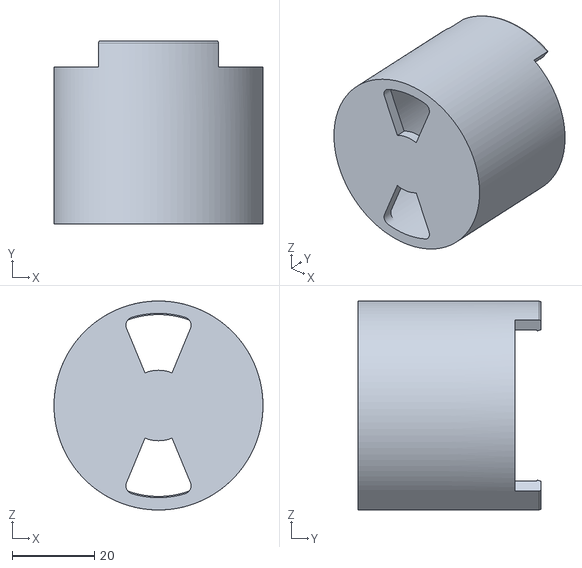
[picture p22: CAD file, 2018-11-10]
Hardware/CAD Parts/STL Files/Ballast Dispenser/v7/Hopper.stl
50.8 x 44.6 x 50.8

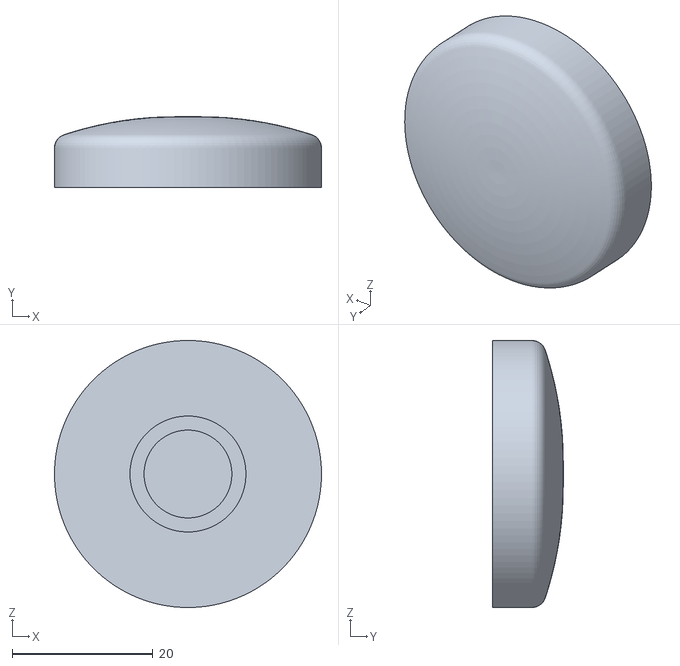
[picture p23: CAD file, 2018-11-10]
Hardware/CAD Parts/STL Files/Helium_Bracket/v2/Helium Stopper 1 in v6.stl
38.0 x 10.0 x 38.0

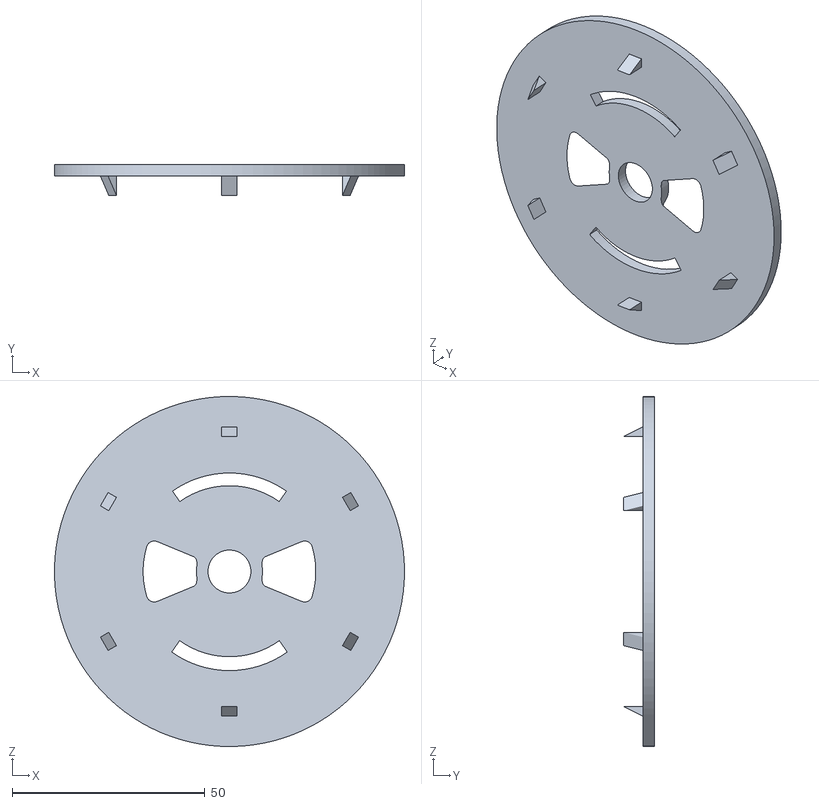
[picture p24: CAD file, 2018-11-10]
Hardware/CAD Parts/STL Files/Ballast Dispenser/v7/Faceplate.stl
90.8 x 8.00 x 90.8

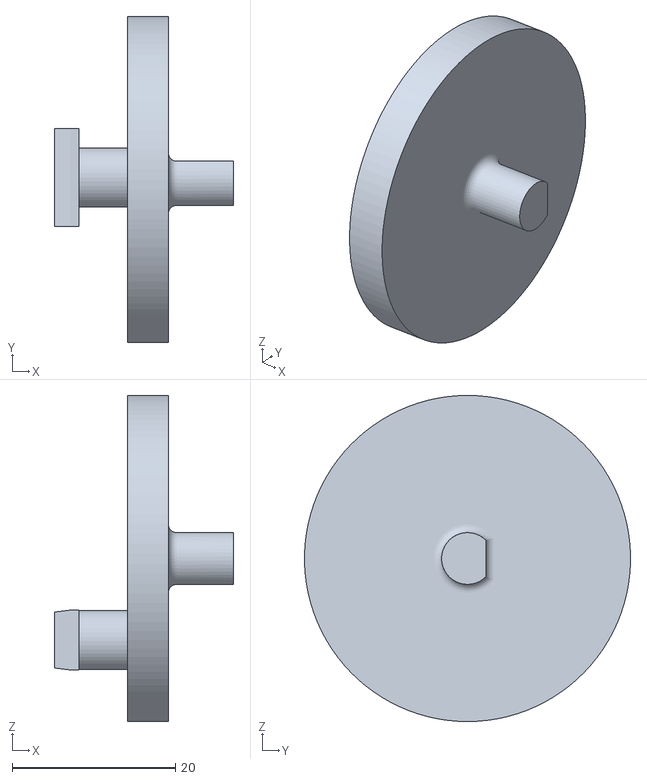
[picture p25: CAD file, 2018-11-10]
Hardware/CAD Parts/STL Files/Helium_Bracket/v2/Helium_Cam.stl
22.0 x 40.0 x 40.0

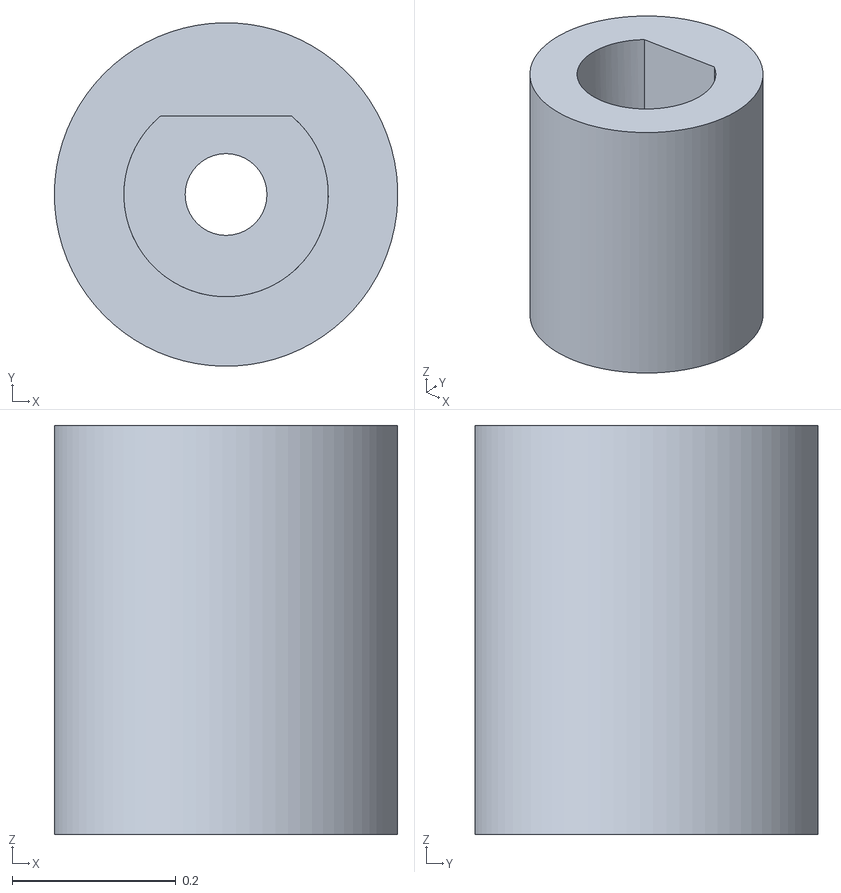
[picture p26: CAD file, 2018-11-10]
Hardware/CAD Parts/STL Files/Servo_Coupler.stl
0.42 x 0.42 x 0.5

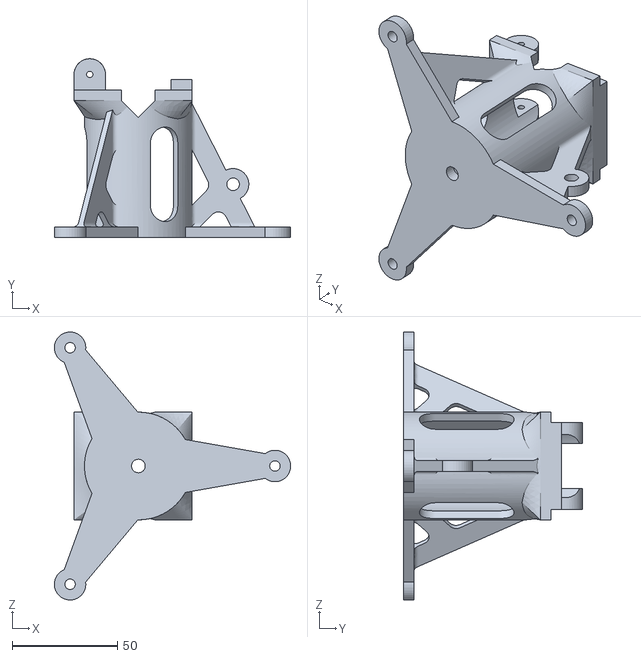
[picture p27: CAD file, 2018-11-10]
Hardware/CAD Parts/STL Files/Helium_Bracket/v2/Printed Bracket 1 in v18.stl
112.5 x 85.0 x 127.5

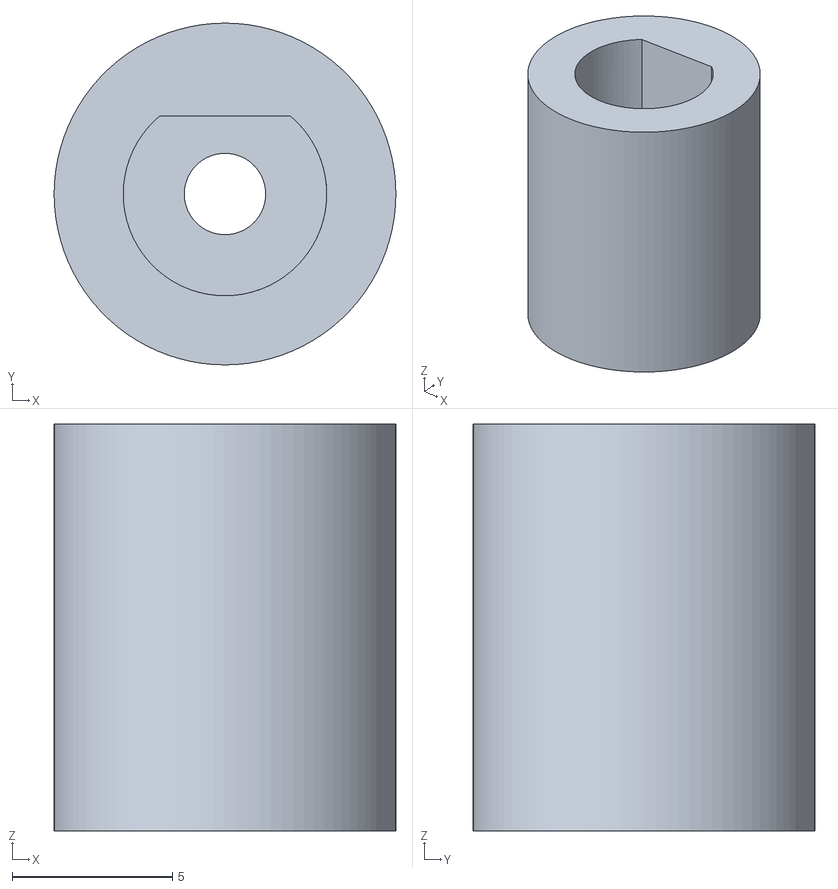
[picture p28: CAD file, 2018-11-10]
Hardware/CAD Parts/STL Files/Servo_Coupler_v3.stl
10.7 x 10.7 x 12.7

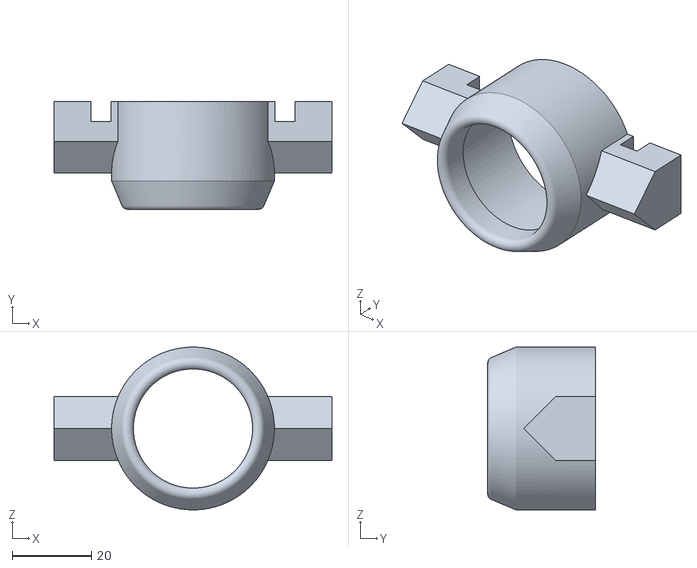
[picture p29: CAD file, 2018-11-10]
Hardware/CAD Parts/STL Files/Helium_Bracket/v2/PVC Fitting 1 in v11.stl
70.0 x 27.1 x 41.0

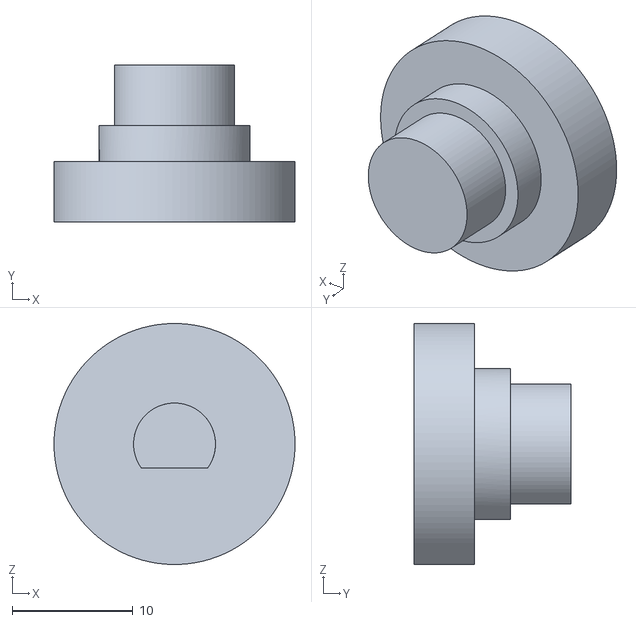
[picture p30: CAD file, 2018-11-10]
Hardware/CAD Parts/STL Files/Helium_Bracket/v2/Helium Attachment End 1 in v3.stl
20.0 x 13.0 x 20.0

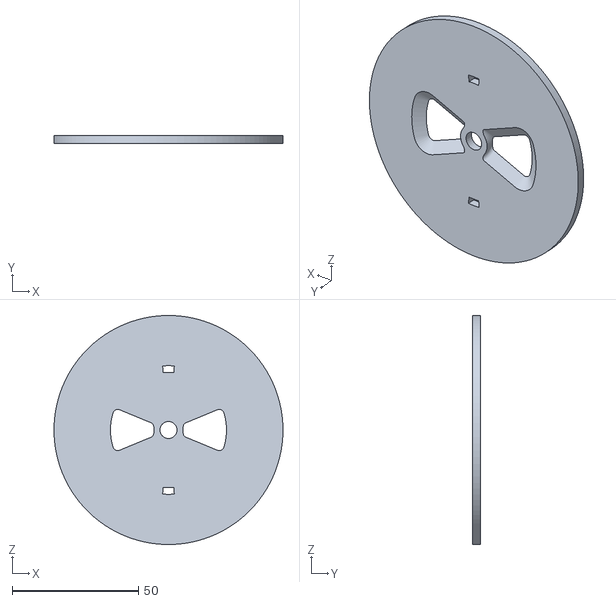
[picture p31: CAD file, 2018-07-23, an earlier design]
Hardware/CAD Parts/STL Files/Ballast Dispenser/v1/Faceplate.stl
90.8 x 3.00 x 90.8

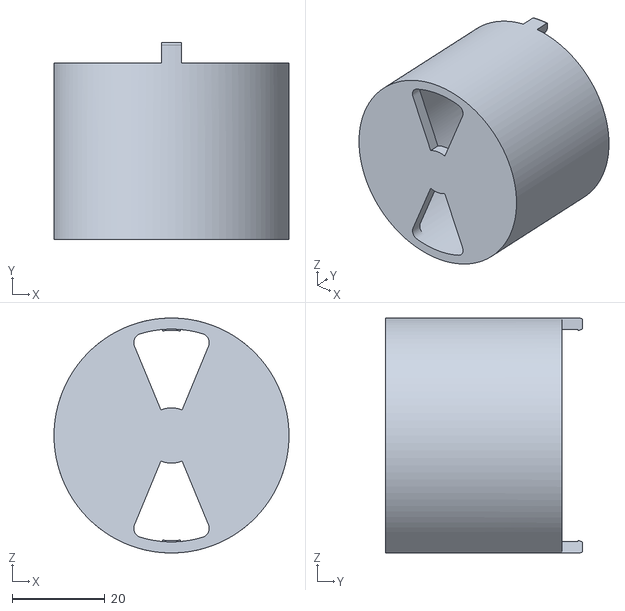
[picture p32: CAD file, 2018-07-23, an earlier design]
Hardware/CAD Parts/STL Files/Ballast Dispenser/v2/Hopper.stl
50.8 x 42.6 x 50.8

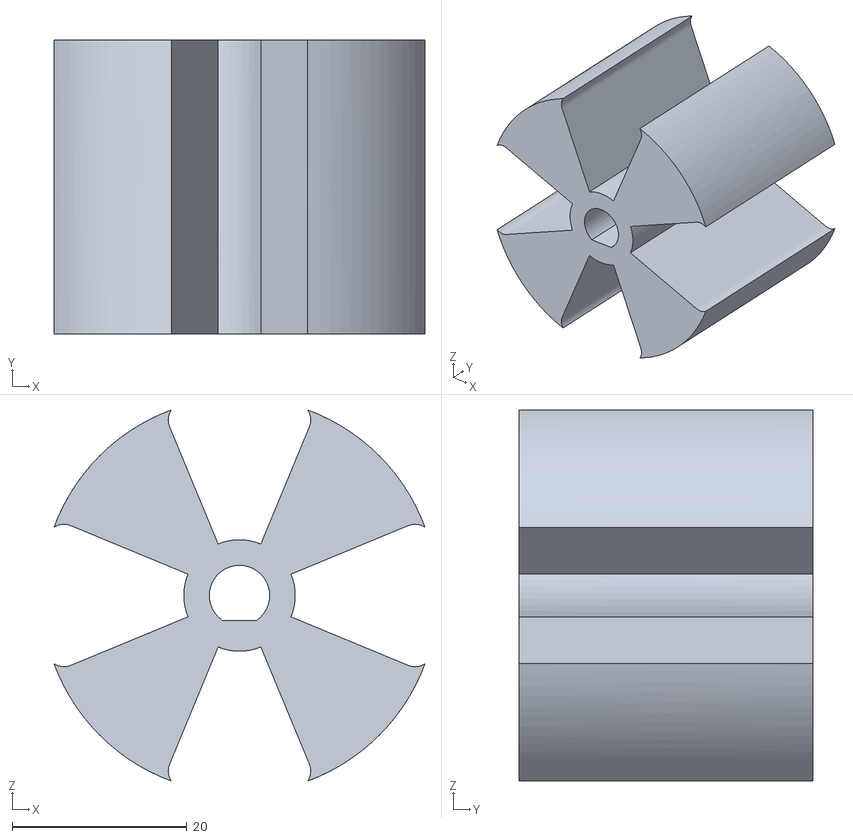
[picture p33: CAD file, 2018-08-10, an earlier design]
Hardware/CAD Parts/STL Files/Ballast Dispenser/v3/Spinner.stl
42.4 x 33.6 x 42.4

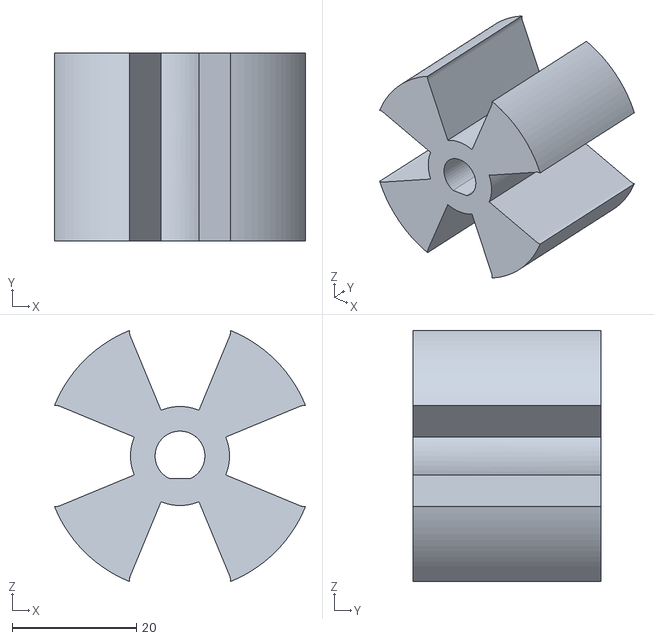
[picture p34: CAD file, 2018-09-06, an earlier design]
Hardware/CAD Parts/STL Files/Ballast Dispenser/v5/Spinner.stl
40.4 x 30.4 x 40.4

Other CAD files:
Hardware/CAD Parts/STL Files/Ballast Dispenser/v4/Faceplate.stl
Hardware/CAD Parts/STL Files/Ballast Dispenser/v6/Faceplate.stl
Hardware/CAD Parts/STL Files/Helium_Bracket/v1/Bracket.stl
Hardware/CAD Parts/STL Files/Servo_Coupler_v2.stl
Hardware/CAD Parts/STL Files/Ballast Dispenser/v1/Hopper.stl
Hardware/CAD Parts/STL Files/Ballast Dispenser/v1/Spinner.stl
Hardware/CAD Parts/STL Files/Ballast Dispenser/v2/Faceplate.stl
Hardware/CAD Parts/STL Files/Ballast Dispenser/v2/Spinner.stl
Hardware/CAD Parts/STL Files/Ballast Dispenser/v3/Faceplate.stl
Hardware/CAD Parts/STL Files/Ballast Dispenser/v3/Hopper.stl
Hardware/CAD Parts/STL Files/Ballast Dispenser/v4/Spinner.stl
Hardware/CAD Parts/STL Files/Ballast Dispenser/v5/Faceplate.stl
Hardware/CAD Parts/STL Files/Ballast Dispenser/v5/Hopper.stl
Hardware/CAD Parts/STL Files/Ballast Dispenser/v6/Hopper.stl
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

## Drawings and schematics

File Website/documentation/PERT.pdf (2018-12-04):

2-4-6 I 2-3-7

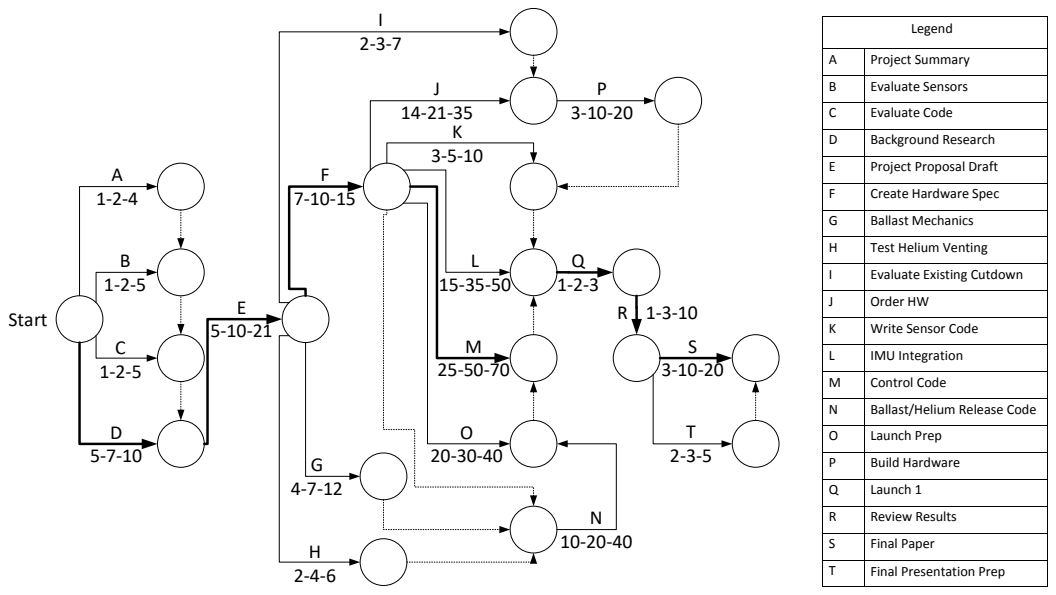
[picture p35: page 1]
Legend; Start

A | Project Summary
B | Evaluate Sensors
C | Evaluate Code
D | Background Research
E | Project Proposal Draft
F | Create Hardware Spec
G | Ballast Mechanics
H | Test Helium Venting
I | Evaluate Existing Cutdown
J | Order HW
K | Write Sensor Code
L | IMU Integration
M | Control Code
N | Ballast/Helium Release Code
O | Launch Prep
P | Build Hardware
Q | Launch 1
R | Review Results

S | Final Paper

T | Final Presentation Prep

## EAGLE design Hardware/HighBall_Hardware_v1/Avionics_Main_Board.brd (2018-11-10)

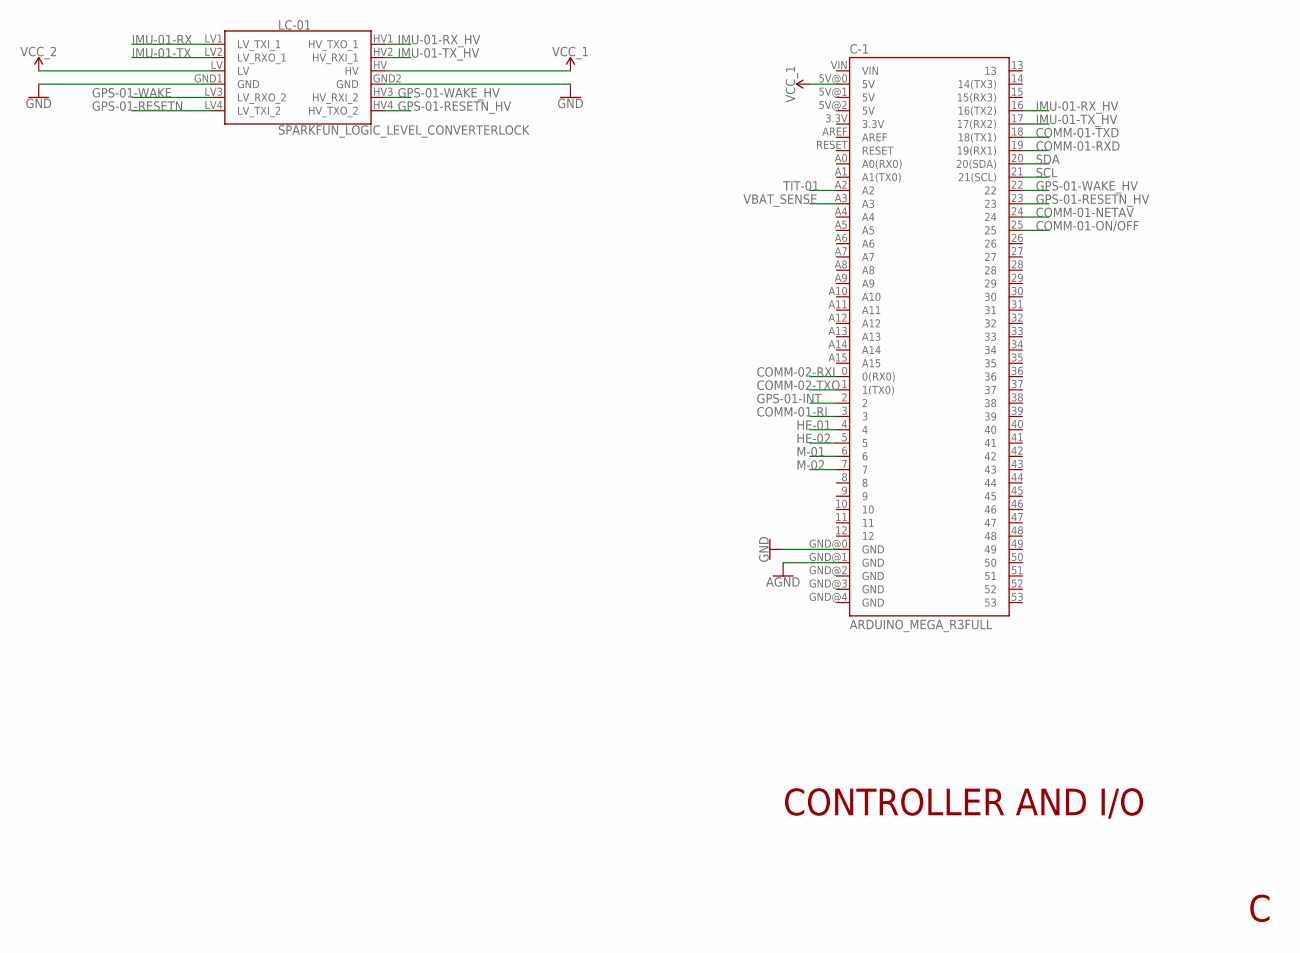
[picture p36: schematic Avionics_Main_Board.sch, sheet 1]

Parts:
C-1: ARDUINO_MEGA_R3FULL; ARDUINO_MEGA
LC-01: SPARKFUN_LOGIC_LEVEL_CONVERTERLOCK; SPARKFUN_LOGIC_LEVEL_CONVERTER_LOCK

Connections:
AGND: C-1.GND@1 (GND); also elsewhere on the board
COMM-01-NETAV: C-1.24; also elsewhere on the board
COMM-01-ON/OFF: C-1.25; also elsewhere on the board
COMM-01-RI: C-1.3; also elsewhere on the board
COMM-01-RXD: C-1.19 (19(RX1)); also elsewhere on the board
COMM-01-TXD: C-1.18 (18(TX1)); also elsewhere on the board
COMM-02-RXI: C-1.0 (0(RX0)); also elsewhere on the board
COMM-02-TXO: C-1.1 (1(TX0)); also elsewhere on the board
GND: C-1.GND@0 (GND), LC-01.GND1 (GND), LC-01.GND2 (GND); also elsewhere on the board
GPS-01-INT: C-1.2; also elsewhere on the board
GPS-01-RESETN: LC-01.LV4 (LV_TXI_2); also elsewhere on the board
GPS-01-RESETN_HV: C-1.23, LC-01.HV4 (HV_TXO_2)
GPS-01-WAKE: LC-01.LV3 (LV_RXO_2); also elsewhere on the board
GPS-01-WAKE_HV: C-1.22, LC-01.HV3 (HV_RXI_2)
HE-01: C-1.4; also elsewhere on the board
HE-02: C-1.5; also elsewhere on the board
IMU-01-RX: LC-01.LV1 (LV_TXI_1); also elsewhere on the board
IMU-01-RX_HV: C-1.16 (16(TX2)), LC-01.HV1 (HV_TXO_1)
IMU-01-TX: LC-01.LV2 (LV_RXO_1); also elsewhere on the board
IMU-01-TX_HV: C-1.17 (17(RX2)), LC-01.HV2 (HV_RXI_1)
M-01: C-1.6; also elsewhere on the board
M-02: C-1.7; also elsewhere on the board
SCL: C-1.21 (21(SCL)); also elsewhere on the board
SDA: C-1.20 (20(SDA)); also elsewhere on the board
TIT-01: C-1.A2; also elsewhere on the board
VBAT_SENSE: C-1.A3; also elsewhere on the board
VCC_1: C-1.5V@0 (5V), LC-01.HV; also elsewhere on the board
VCC_2: LC-01.LV; also elsewhere on the board

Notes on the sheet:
CONTROLLER AND I/O

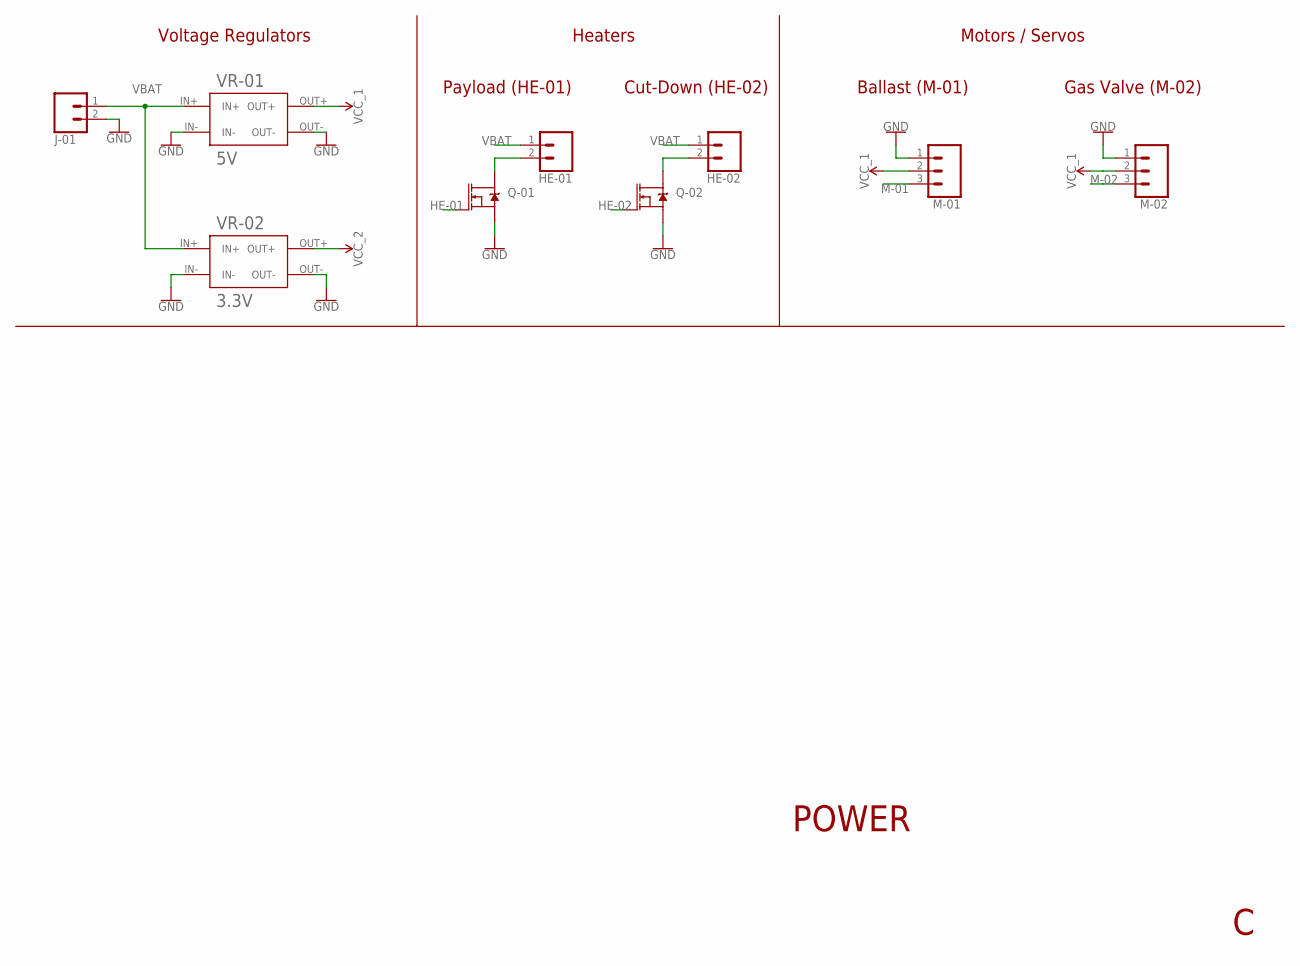
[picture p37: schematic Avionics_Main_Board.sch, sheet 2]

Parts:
HE-01, HE-02: CONN_02LOCK; 1X02_LOCK
J-01: CONN_023.5MM_LOCK; SCREWTERMINAL-3.5MM-2_LOCK
M-01, M-02: CONN_03LOCK; 1X03_LOCK
Q-01, Q-02: MOSFET-NCH-FQP30N06L; TO220V
VR-01: 5V; RIORAND_LM2596_BREAKOUT
VR-02: 3.3V; RIORAND_LM2596_BREAKOUT

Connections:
GND: J-01.2, M-01.1, M-02.1, Q-01.3 (S), Q-02.3 (S), VR-01.IN-, VR-01.OUT-, VR-02.IN-, VR-02.OUT-; also elsewhere on the board
HE-01: Q-01.1 (G); also elsewhere on the board
HE-01_OUT: HE-01.2, Q-01.2 (D)
HE-02: Q-02.1 (G); also elsewhere on the board
HE-02_OUT: HE-02.2, Q-02.2 (D)
M-01: M-01.3; also elsewhere on the board
M-02: M-02.3; also elsewhere on the board
VBAT: HE-01.1, HE-02.1, J-01.1, VR-01.IN+, VR-02.IN+; also elsewhere on the board
VCC_1: M-01.2, M-02.2, VR-01.OUT+; also elsewhere on the board
VCC_2: VR-02.OUT+; also elsewhere on the board

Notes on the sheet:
Voltage Regulators
Heaters
Cut-Down (HE-02)
Payload (HE-01)
Motors / Servos
Gas Valve (M-02)
Ballast (M-01)
POWER

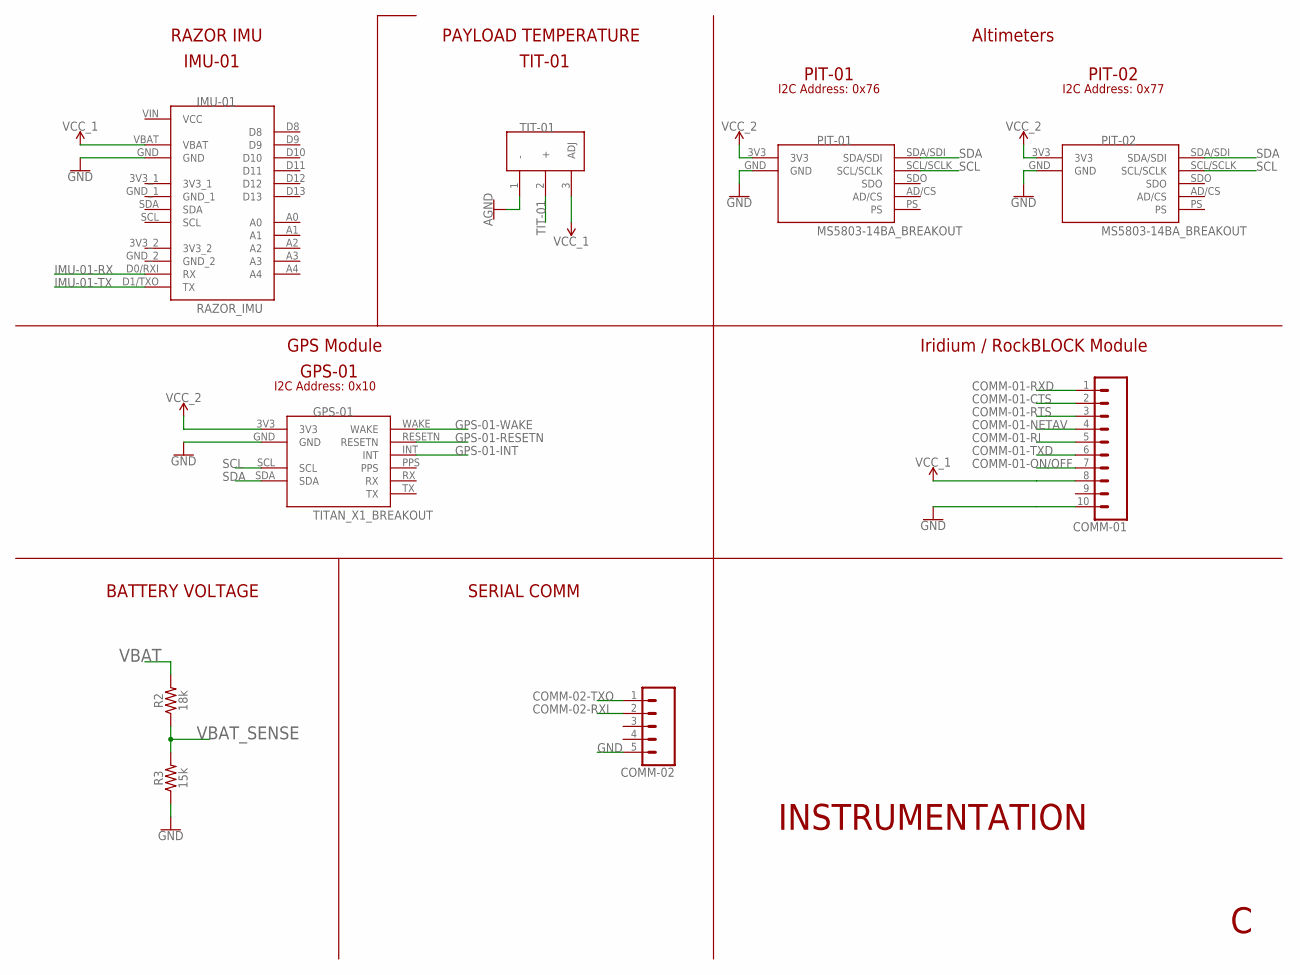
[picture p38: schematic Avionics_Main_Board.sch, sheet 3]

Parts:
COMM-01: CONN_10"; 1X10
COMM-02: CONN_05LOCK; 1X05_LOCK
GPS-01: TITAN_X1_BREAKOUT; QWIIC_TITAN_X1_BREAKOUT
IMU-01: RAZOR_IMU
PIT-01, PIT-02: MS5803-14BA_BREAKOUT
R2: 18k; AXIAL-0.3
R3: 15k; AXIAL-0.3
TIT-01: LM335TO-92; TO92

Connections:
5V: TIT-01.3 (ADJ)
AGND: TIT-01.1 (-); also elsewhere on the board
COMM-01-CTS: COMM-01.2
COMM-01-NETAV: COMM-01.4; also elsewhere on the board
COMM-01-ON/OFF: COMM-01.7; also elsewhere on the board
COMM-01-RI: COMM-01.5; also elsewhere on the board
COMM-01-RTS: COMM-01.3
COMM-01-RXD: COMM-01.1; also elsewhere on the board
COMM-01-TXD: COMM-01.6; also elsewhere on the board
COMM-02-RXI: COMM-02.2; also elsewhere on the board
COMM-02-TXO: COMM-02.1; also elsewhere on the board
GND: COMM-01.10, COMM-02.5, GPS-01.GND, IMU-01.GND, PIT-01.GND, PIT-02.GND, R3.P$1 (1); also elsewhere on the board
GPS-01-INT: GPS-01.INT; also elsewhere on the board
GPS-01-RESETN: GPS-01.RESETN; also elsewhere on the board
GPS-01-WAKE: GPS-01.WAKE; also elsewhere on the board
IMU-01-RX: IMU-01.D0/RXI (RX); also elsewhere on the board
IMU-01-TX: IMU-01.D1/TXO (TX); also elsewhere on the board
SCL: GPS-01.SCL, PIT-01.SCL/SCLK, PIT-02.SCL/SCLK; also elsewhere on the board
SDA: GPS-01.SDA, PIT-01.SDA/SDI, PIT-02.SDA/SDI; also elsewhere on the board
TIT-01: TIT-01.2 (+); also elsewhere on the board
VBAT: R2.P$2 (2); also elsewhere on the board
VBAT_SENSE: R2.P$1 (1), R3.P$2 (2); also elsewhere on the board
VCC_1: COMM-01.8, IMU-01.VBAT; also elsewhere on the board
VCC_2: GPS-01.3V3, PIT-01.3V3, PIT-02.3V3; also elsewhere on the board

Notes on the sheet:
RAZOR IMU
IMU-01
PAYLOAD TEMPERATURE
TIT-01
Altimeters
PIT-01
PIT-02
I2C Address: 0x76
I2C Address: 0x77
GPS Module
GPS-01
I2C Address: 0x10
INSTRUMENTATION
Iridium / RockBLOCK Module
BATTERY VOLTAGE
SERIAL COMM

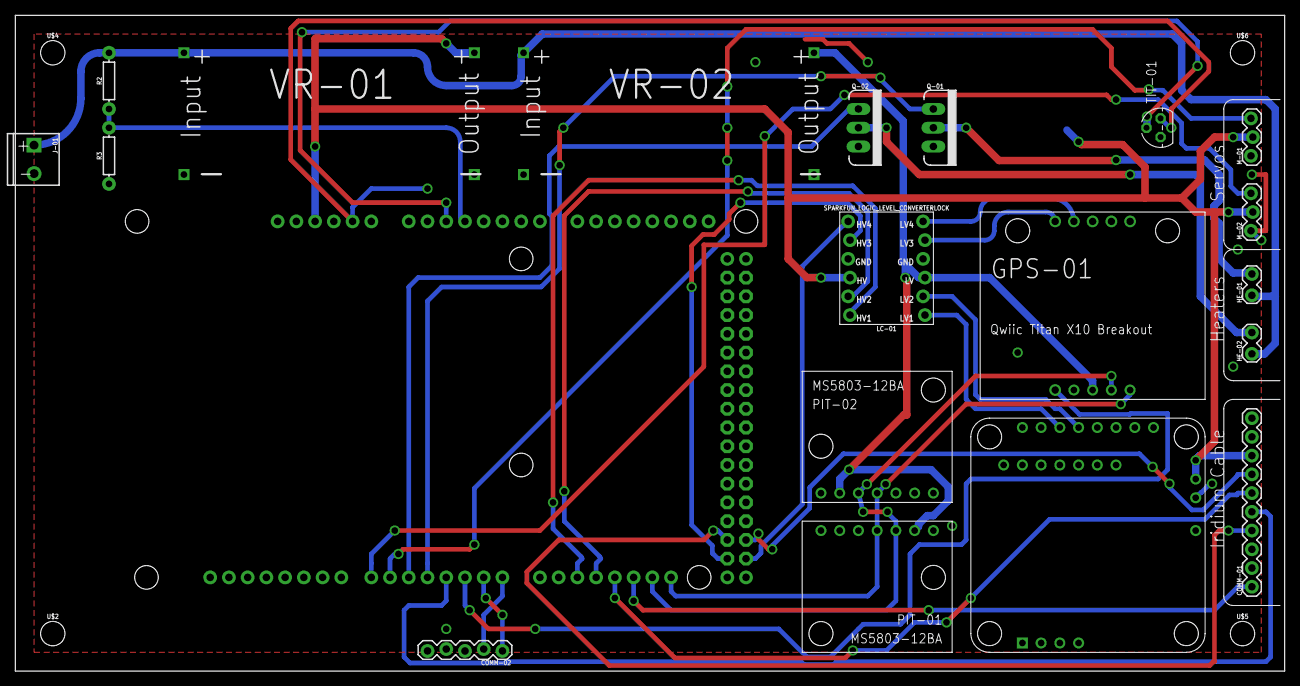
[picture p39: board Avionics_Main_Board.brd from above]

Board: 2 copper layers, 172.1 x 88.9 mm, 24 parts (1 on the bottom side), 31 nets.

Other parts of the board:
U$2, U$4, U$5, U$6: STAND-OFF

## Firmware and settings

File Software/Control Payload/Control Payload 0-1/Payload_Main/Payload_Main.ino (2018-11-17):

#include "Sensors.h"
#include "Actuators.h"
#include "Communications.h"
#include "Control.h"
#include "State_Machine.h"
#include <Servo.h>

#define PRESSURE_01_ADR 0x76
#define PRESSURE_02_ADR 0x77
#define AUTO 0
#define MANUAL 3

#define ControlPeriod 300

int ballastUsed = 0;
int heliumUsed = 0;

#define CUT_DOWN 5

#define d2r (M_PI / 180.0)

//temperature_sensor temp;

pressure_sensor pressure1(ADDRESS_HIGH);
pressure_sensor pressure2(ADDRESS_LOW);

//IMU imu;

GPS gps;

//altitude_control control;
altitude_control control;
helium_ballast action;

// servo setup
struct Helium_Data helium_servo;
int ballast_count;

unsigned long controlTime;
unsigned long conditionTime;
unsigned long sendTime;
//unsigned long timer1;
//bool hel = true;
//bool bal = true;

float temperature1=0;
float temperature2=0;
float temperature=0;

float prs1;
float prs2;
float prs;
float altitude;
float altitude1;
float altitude2;
float velocity;
//IMU_Data imu_data;
GPS_Data gps_data;

double initial_lat;     
double initial_long;

struct Incoming_Data incoming;
struct Outgoing_Data outgoing;
bool message_sent;

void setup()
{
  //Setup and turn off cutdown mechanism
  pinMode(CUT_DOWN,OUTPUT);
  analogWrite(CUT_DOWN,0);
  Serial.begin(9600);
  
  Serial.println("Before Pressure");
  pressure1.initialize_sensor();
  pressure2.initialize_sensor();
  Serial.println("After Pressure");

  Serial.println("Before GPS");
  gps.create_GPS();
  Serial.println("After GPS");
/*
  Serial.println("Before IMU");
  imu.initialize_IMU();
  Serial.println("After IMU");
*/
  
  setup_Actuators();
  helium_servo.ventTime = controlTime;
  helium_servo.position = 0;
  helium_servo.open = false;
  ballast_count = 0;

  prs1 = pressure1.read_pressure();
  prs2 = pressure2.read_pressure();
  altitude =  altitudeCalc(pressure1.find_altitude(prs1), pressure2.find_altitude(prs2));

  temperature1 = pressure1.read_temperature();
  temperature2 = pressure2.read_temperature();
  temperature = (temperature1 + temperature2) / 2.0;

  gps_data = gps.read_GPS();         
  initial_lat = gps.get_lat();    
  initial_long = gps.get_long();
  
  setup_Communications();
  incoming.update_rate = 120;
  incoming.manual_adjust = 0;
  incoming.control_mode = MANUAL;
  incoming.cutdown = 0;
  incoming.hel_alpha = 0;
  incoming.hel_beta = 0;
  incoming.hel_gamma = 0;
  incoming.bal_alpha = 0;
  incoming.bal_beta = 0;
  incoming.bal_gamma = 0;
  incoming.cutdown = 0;
  
  message_sent = false;

  controlTime = millis();
  conditionTime = controlTime;
  sendTime = controlTime;
//  timer1 = controlTime;
}


void loop()
{
  //Serial.println("in loop");
  
  //TODO: check communication (maybe output a struct that contains changes (manual mode, cutdown, etc))
  //TODO: deal with mode change
  //TODO: deal with cutdown
  //TODO: deal with anything else that would change
  //check current conditions

  if((millis() - conditionTime)/1000 >= 5){//should we make this a variable time?
    //temperature = temp.read_temp();

    gps_data = gps.read_GPS();
    Serial.println("GPS Altitude = " + String(gps_data.altitude));
    Serial.println("GPS latitude = " + String(gps_data.latitude));
    Serial.println("GPS longitude = " + String(gps_data.longitude));
    Serial.println("GPS satellites = " + String(gps_data.satellites));
    Serial.println("");

    prs1 = pressure1.read_pressure();
    prs2 = pressure2.read_pressure();
    altitude1 = pressure1.find_altitude(prs1);
    altitude2 = pressure2.find_altitude(prs2);
    Serial.println("");
    Serial.println("Pressure Sensor Altitude 1 = " + String(altitude1));
    Serial.println("Presure Sensor Altitude 2 = " + String(altitude2));
    Serial.println("Pressure Sensor Pressure 1 = " + String(prs1));
    //Serial.println("Pressure Sensor Baseline 1 = " + String(pressure1.get_baseline()));
    Serial.println("Pressure Sensor Pressure 2 = " + String(prs2));
    //Serial.println("Pressure Sensor Baseline 2 = " + String(pressure2.get_baseline()));
    velocity = verticalVelocityCalc(altitudeCalc(altitude1, altitude2), altitude, millis(), conditionTime);
    Serial.println("Pressure Sensor Velocity = " + String(velocity));
    conditionTime = millis();
    altitude = altitudeCalc(altitude1, altitude2);//need to do error checking, this was a quick fix
    Serial.println("Pressure Sensor Altitude = " + String(altitude));

    temperature1 = pressure1.read_temperature();
    temperature2 = pressure2.read_temperature();
    temperature = (temperature1 + temperature2) / 2.0;
    Serial.println("");
    Serial.println("Temperature 1 = " + String(temperature1));
    Serial.println("Temperature 2 = " + String(temperature2));
    Serial.println("Temperature = " + String(temperature));
/*
    imu_data = imu.read_IMU();
    Serial.println("IMU Upward Accel = " + String(imu_data.accelUp));
    Serial.println("IMU Horizontal Accel = " + String(imu_data.accelHoriz));
    Serial.println("IMU Direction = " + String(imu_data.direction));
*/
  }
  
  // send message
  if ((millis() - sendTime) / 1000 >= incoming.update_rate) {
    Serial.println("Start Send");
    // Temperature Data
    outgoing.temperature = temperature; // get temperature
    // Pressure Data

    if (abs(prs1 - prs2) > .25 * prs1) {
      if (abs(altitude1 - altitude) > abs(altitude2 - altitude)) {
        prs = prs2;
      } else {
        prs = prs2;
      }
    } else {
      prs = (prs1 + prs2) / 2;
    }

    outgoing.pressure = prs; // get pressure
    // Acceleration Data
    // GPS Data
    outgoing.altitude = gps_data.altitude;
    outgoing.latitude = gps_data.latitude;
    outgoing.longitude = gps_data.longitude;
    // Velovity Data
    outgoing.vel = velocity;
    // Ballast Data
    outgoing.ballast = ballastUsed;
    // Helium Data
    outgoing.helium = heliumUsed;
    // State Data
    outgoing.state = 0; // state machine defunct
    // Control Mode Data
    outgoing.control_mode = incoming.control_mode;
    // Emergency Data
    outgoing.emergency = 0; // no emergency settings

    encode_message(&outgoing);
    message_sent = call_iridium(10);
    delay(1000);

    bool new_data;
    new_data = decode_message(&incoming);

    if (new_data) {
      Serial.println("*");
      Serial.println("*");
      Serial.println("*");
      Serial.println("Altitude: " + String(incoming.altitude));
      Serial.println("Alt Buffer: " + String(incoming.altitude_buffer));
      Serial.println("Latitude: " + String(incoming.lat_deg));
      Serial.println("Longitude: " + String(incoming.long_deg));
      Serial.println("Update Rate: " + String(incoming.update_rate));
      Serial.println("Max Velocity: " + String(incoming.max_velocity));
      Serial.println("Temperature: " + String(incoming.temp));
      Serial.println("Control: " + String(incoming.control_mode));
      Serial.println("Manual Amount: " + String(incoming.manual_amount));
      
      Serial.println("Helium Alpha: " + String(incoming.hel_alpha));
      Serial.println("Helium Beta: " + String(incoming.hel_beta));
      Serial.println("Helium Gamma: " + String(incoming.hel_gamma));
      Serial.println("Ballast Alpha: " + String(incoming.bal_alpha));
      Serial.println("Ballast Beta: " + String(incoming.bal_beta));
      Serial.println("Ballast Gamma: " + String(incoming.bal_gamma));
      Serial.println("Cutdown: " + String(incoming.cutdown));
      Serial.println("*");
      Serial.println("*");
      Serial.println("*");
  
      control.set_min_altitude(incoming.altitude - incoming.altitude_buffer/2);
      control.set_max_altitude(incoming.altitude + incoming.altitude_buffer/2);
      
      control.set_min_velocity(incoming.max_velocity);
      // control.set_min_accel(incoming.altitude);
      
      control.set_bal_alpha(incoming.bal_alpha);
      control.set_bal_beta(incoming.bal_beta);
      control.set_bal_gamma(incoming.bal_gamma);
      control.set_hel_alpha(incoming.hel_alpha);
      control.set_hel_beta(incoming.hel_beta);
      control.set_hel_gamma(incoming.hel_gamma);
    }

    sendTime = millis();
  }

  //run control algorithm every 5 minutes
  if ((millis() - controlTime) / 1000 >= ControlPeriod && incoming.control_mode == AUTO) { //should we make this a variable time?
    // fill struct with ballast and helium scores
    //action = control.get_action(altitude, velocity, imu_data.accelUp);
    action = control.get_action(altitude, velocity, 0);
    if (action.helium > 0) {
      if (action.helium > ControlPeriod) {
        action.helium = ControlPeriod;
      }
      // set helium vent end time
      helium_servo.ventTime = (unsigned long)(action.helium*1000) + millis(); 
      // update helium used register
      heliumUsed = heliumUsed + action.helium;
      // open helium 80%
      openHeliumServo (&helium_servo, .8);
    } else if (action.ballast > 0) {
      if (action.ballast > ControlPeriod/2) {
        action.ballast= ControlPeriod/2;
      }
      // set count of how many ballast drops during this control cycle
      ballast_count = (int) (action.ballast);
    }
  } else if (incoming.control_mode == MANUAL && incoming.manual_adjust) {
    // unlatch manual adjust bit
    incoming.manual_adjust = false;
    // check whether adjustment is for helium or ballast
    if (incoming.manual_select) {
      // set count of how many ballast drops during this control cycle
      ballast_count = (int) (incoming.manual_amount);
      Serial.println("set ballast count");
    } else {
      // set helium vent end time
      helium_servo.ventTime = (unsigned long)(incoming.manual_amount*1000) + millis(); 
      // open helium 80%
      Serial.println("open helium");
      openHeliumServo (&helium_servo, 1);
      // update helium used register
      heliumUsed = heliumUsed + incoming.manual_amount;
    }
  }

//  if ((millis() - timer1)/1000 > 60  && hel )  {
//    hel = false;
//    Serial.println("adjust helium");
//    incoming.control_mode = MANUAL;
//    incoming.manual_adjust = true;
//    incoming.manual_select = false;
//    incoming.manual_amount = 5;
//  }
//
//  if ((millis() - timer1)/1000 > 70  && bal )  {
//    bal = false;
//    Serial.println("adjust ballast");
//    incoming.control_mode = MANUAL;
//    incoming.manual_adjust = true;
//    incoming.manual_select = true;
//    incoming.manual_amount = 5;
//  }

  // Drop ballast if currently requested
  if (ballast_count > 0) {
    // drop ballast and decrement the count
    runBallastServo();
    Serial.println(ballast_count);
    ballast_count = ballast_count - 1;
    // update helium used register
    ballastUsed = ballastUsed + 1;
  }

  // Close helium vent after alloted time
  if (helium_servo.ventTime < millis()  && helium_servo.open) {
    // close the helium vent after time runs out
    Serial.println("close helium");
    closeHeliumServo (&helium_servo);
  }
  
  // Cutdown after getting signal
  if (incoming.cutdown) {
    // cutdown
    cut_down();
  }
}

float verticalVelocityCalc(float altitudeNew, float altitudeOld, unsigned long timeNew, unsigned long timeOld){
  float velocity = (altitudeNew - altitudeOld) / (timeNew-timeOld) * 1000;
  return(velocity);
}

float altitudeCalc(float alt1, float alt2) {
  float alt = (alt1 + alt2)/2;
  return(alt);
}

void auto_cutdown(double initial_lat, double initial_long, double lat2, double long2)
{
    float dlong = (long2 - initial_long) * d2r;
    float dlat = (lat2 - initial_lat) * d2r;
    float a = pow(sin(dlat/2.0), 2) + cos(initial_lat*d2r) * cos(lat2*d2r) * pow(sin(dlong/2.0), 2);
    float c = 2 * atan2(sqrt(a), sqrt(1-a));
    float d = 3956 * c; 
  if(d>100.0)        //cutdown if distance is greater than 100.0 miles
  {
    cut_down();
  }  
}

void cut_down(){
  analogWrite(CUT_DOWN,105);
  delay(40000);
  analogWrite(CUT_DOWN,0);
}

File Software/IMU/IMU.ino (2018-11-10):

#include <SparkFunMPU9250-DMP.h>
#include<math.h>
float zCalibration[3];
float xCalibration[3];
float yCalibration[3];
//IMU
MPU9250_DMP imu;

float zAcceleration;
float horizontalAcceleration;
float direction;

boolean output_single_on = false;
boolean output_comms_test = false;

void setup()
{
  SerialUSB.begin(115200); //set baud rate
  Serial.begin(9600);
  // Check communication with IMU
  while(imu.begin() != INV_SUCCESS)
  {
      SerialUSB.println("Unable to connect with IMU.");
      delay(5000);
  }//end while display
  
  //enable 6-axis quaternion outpu
  imu.dmpBegin(DMP_FEATURE_SEND_RAW_ACCEL | DMP_FEATURE_SEND_CAL_GYRO | DMP_FEATURE_6X_LP_QUAT | DMP_FEATURE_GYRO_CAL, 50);//check sampling rate

  //enable XYZ magnetometer for absolute orientation determination
  imu.setSensors(INV_XYZ_GYRO | INV_XYZ_ACCEL | INV_XYZ_COMPASS);
  imu.setGyroFSR(2000);
  imu.setAccelFSR(2);
  imu.setSampleRate(50);
  imu.setCompassSampleRate(50);//check sampling rate
  imu.update(UPDATE_ACCEL);

  //set calibration
  zCalibration[0]=0; //x
  zCalibration[1]=0; //y
  zCalibration[2]=1; //z

  xCalibration[0] = 1; //x
  xCalibration[1] = 0; //y
  xCalibration[2] = 0; //z

  yCalibration[0] = 0; //x
  yCalibration[1] = 1; //y
  yCalibration[2] = 0; //z
  
}//end setup_IMU_01

void loop()
{
  // Can add comms test code as an additional command here
  if (Serial.available() > 0) {
    if (Serial.read() == '#') { // Start of control message
      int command = Serial.read(); // read command
      if (command == 'f') { // Request Data
        output_single_on = true;
      } else if (command == 'c') { // Reply to Comms test
        output_comms_test = true;
      }
    }
    Serial.flush();
  }
  //SerialUSB.flush();
  /*if(Serial.available() > 0){
    comm = Serial.read();
    if(comm == '1'){
      Serial.print('2');//may change back to '1'
    }
    else if (comm == '0') {
      Serial.print('0');
    } else if (comm == '2') {
      exportValues(zAcceleration, horizontalAcceleration, direction);
    }
  } */
  //IMU_OUTPUT updateValues;
  if ( imu.fifoAvailable() )//if there is new data
  {
    if (imu.dmpUpdateFifo() == 0)//update data
    {
      //update orientation
      //SerialUSB.println("inif");
      imu.update(UPDATE_ACCEL | UPDATE_GYRO | UPDATE_COMPASS);
      imu.computeEulerAngles(false); //output in radians
      calculateValues();
      }
  }

  if (output_single_on) exportValues(zAcceleration, horizontalAcceleration, direction); // send if data is requested
  if (output_comms_test) commsReply();

  output_single_on = false;
  output_comms_test = false;
  return;
}

static void calculateAngles(float qw, float qx, float qy, float qz, double& roll, double& pitch, double& yaw){
  //double qy2 = qy * qy;
  //calculate roll
  float t0 = +2.0 * (qw * qx + qy * qz);
  float t1 = +1.0 - 2.0 * ( qx * qx + qy*qy);
  roll = atan2(t0,t1);

  //calculate pitch
  float t2 = +2.0 * (qw * qy  - qz * qx);
  if(fabs(t2) >= 1){
    pitch = copysign(M_PI/2, t2);
  }
  else{
    pitch = asin(t2);
  }

  //SerialUSB.println("T2 = " + String(t2));
  //SerialUSB.println("qw  " + String(qw) +  "   qx  " + String(qx) +  "   qy  " + String(qy) +  "   qz  " + String(qz));
  float t3 = +2.0 * (qw * qz + qx * qy);
  float t4 = +1.0 - 2.0 * (qy*qy + qz * qz);
  yaw = atan2(t3, t4);

}

void calculateValues(){

  float zOrientation[3];
  float xOrientation[3];
  float yOrientation[3];

  double theta; //roll
  double psi; //pitch
  double phi; //yaw

  calculateAngles(imu.calcQuat(imu.qw), imu.calcQuat(imu.qx), imu.calcQuat(imu.qy), imu.calcQuat(imu.qz), theta, psi, phi);

  float qi = imu.calcQuat(imu.qx);
  float qj = imu.calcQuat(imu.qy);
  float qk = imu.calcQuat(imu.qz);
  float qr = imu.calcQuat(imu.qw);

  //calculate rotation from calibration using pitch - roll - yaw roration matrix
  zOrientation[0] = zCalibration[0] * (cos(theta) * cos(phi)) + zCalibration[1] * (cos(theta) * sin(phi)) - zCalibration[2] * sin(theta);
  zOrientation[1] = zCalibration[0] * (sin(psi) * sin(theta) * cos(phi) - cos(psi) * sin(phi)) + zCalibration[1] * (sin(psi) * sin(theta) * sin(phi) + cos(psi) * cos(phi)) + zCalibration[2] * (cos(theta) * sin(psi));
  zOrientation[2] = zCalibration[0] *	(cos(psi) * sin(theta) * cos(phi) + sin(psi) * sin(phi)) + zCalibration[1] * (cos(psi) * sin(theta) * sin(phi) - sin(psi) * cos(phi)) + zCalibration[2] * cos(theta) * cos(psi);

  xOrientation[0] = xCalibration[0] * (cos(theta) * cos(phi)) + xCalibration[1] * (cos(theta) * sin(phi)) - xCalibration[2] * sin(theta);
  xOrientation[1] = xCalibration[0] * (sin(psi) * sin(theta) * cos(phi) - cos(psi) * sin(phi)) + xCalibration[1] * (sin(psi) * sin(theta) * sin(phi) + cos(psi) * cos(phi)) + xCalibration[2] * (cos(theta) * sin(psi));
  xOrientation[2] = xCalibration[0] *	(cos(psi) * sin(theta) * cos(phi) + sin(psi) * sin(phi)) + xCalibration[1] * (cos(psi) * sin(theta) * sin(phi) - sin(psi) * cos(phi)) + xCalibration[2] * cos(theta) * cos(psi);

  yOrientation[0] = yCalibration[0] * (cos(theta) * cos(phi)) + yCalibration[1] * (cos(theta) * sin(phi)) - yCalibration[2] * sin(theta);
  yOrientation[1] = yCalibration[0] * (sin(psi) * sin(theta) * cos(phi) - cos(psi) * sin(phi)) + yCalibration[1] * (sin(psi) * sin(theta) * sin(phi) + cos(psi) * cos(phi)) + yCalibration[2] * (cos(theta) * sin(psi));
  yOrientation[2] = yCalibration[0] *	(cos(psi) * sin(theta) * cos(phi) + sin(psi) * sin(phi)) + yCalibration[1] * (cos(psi) * sin(theta) * sin(phi) - sin(psi) * cos(phi)) + yCalibration[2] * cos(theta) * cos(psi);

  //calculate dot product to project acceleration onto orientation
  zAcceleration = -1*(zOrientation[0] * -1*imu.calcAccel(imu.ay) + zOrientation[1] * -1* imu.calcAccel(imu.ax) + zOrientation[2] * imu.calcAccel(imu.az));
  float xAcceleration = -1*(xOrientation[0] * -1*imu.calcAccel(imu.ay) + xOrientation[1] * -1* imu.calcAccel(imu.ax) + xOrientation[2] * imu.calcAccel(imu.az));
  float yAcceleration = -1*(yOrientation[0] * -1*imu.calcAccel(imu.ay) + yOrientation[1] * -1* imu.calcAccel(imu.ax) + yOrientation[2] * imu.calcAccel(imu.az));

  direction;

  if(xAcceleration < 0){
    direction = atan(yAcceleration/xAcceleration)*180/M_PI + 180;
  }
  else if((xAcceleration > 0) && (yAcceleration >= 0)){
    direction = atan(yAcceleration/xAcceleration)*180/M_PI;
  }
  else if((xAcceleration > 0) && (yAcceleration <= 0)){
    direction = atan(yAcceleration/xAcceleration)*180/M_PI + 360;
  }
  else if(xAcceleration == 0){
    direction = yAcceleration > 0 ? M_PI/2 : 3*M_PI/2;
  }
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

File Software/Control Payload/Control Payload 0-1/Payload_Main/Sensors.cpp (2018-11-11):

#include <SparkFun_MS5803_I2C.h>
#include <Wire.h>

#include "Sensors.h"
#include <stdlib.h>
#include <string.h>
#include <TextFinder.h>

// Temperature Sensor {{{
#define TEMPERATURE_DEFAULT_CAL 100.0
#define TEMPERATURE_DEFAULT_PIN A2
// Default Constructor, assumes 100 cal and pin A2
temperature_sensor::temperature_sensor() {
  set_cal(TEMPERATURE_DEFAULT_CAL); // 10 mV <-> 1 Kelvin
  set_pin(TEMPERATURE_DEFAULT_PIN);
}

// Constructor, set cal and pin #
temperature_sensor::temperature_sensor(float _cal, int _pin) {
  set_cal(_cal);
  set_pin(_pin);
}

float temperature_sensor::read_temp() {
  /* Reads the analog output level and converts to temperature data
   *
   * Returns
   * -------
   *  float: Temperature measured by the sensor
   */
  float voltage = (5.0 / 1024.0) * ((float)analogRead(get_pin()));
  Serial.println("Temperature Voltage = " + String(voltage));
  return((voltage - 0.5) * 100);
}

// get functions for each member variable
float temperature_sensor::get_cal() {return(calibration);}

int temperature_sensor::get_pin() {return(pin);}

// set functions for each member variable
void temperature_sensor::set_cal(float _cal) {
  calibration = _cal;
  return;
}

void temperature_sensor::set_pin(int _pin) {
  pin = _pin;
  return;
}

// }}}
// Pressure Sensor {{{
//#define PRESSURE_DEFAULT_ADDR 0x76
// Default constructor, assumes address=0x76
pressure_sensor::pressure_sensor() : sensor(ADDRESS_HIGH) {
  //initialize_sensor();
}

// Constructor, user provided address
pressure_sensor::pressure_sensor(ms5803_addr _addr) : sensor(_addr) {
  //initialize_sensor();
}

// Constructor, user provided sensor
/*pressure_sensor::pressure_sensor(MS5803& _sensor) {
  // This is not the recommended method of interacting with this class.
  // Provided for edge use cases
  sensor = _sensor;
  initialize_sensor();
}*/

float pressure_sensor::read_pressure() {
  /* Reads the current pressure
   *
   * Returns
   * -------
   *  float: current pressure read by the sensor
   */
  return(sensor.getPressure(ADC_4096));
}

float pressure_sensor::find_altitude(float P) {
  /* Determines the current altitude from a baseline
   *
   * Parameters
   * ----------
   * P : float
   *    Current absolute pressure
   * 
   * Returns
   * -------
   *  float: current altitude above baseline in feet
   */
  //Serial.println("Altitude pressure = " + String(P));
  // altitude calculation from sparkfun example
  float alt_meters = 44330.0*(1-pow(P/get_baseline(),1/5.255));
  //Serial.println("Altitude_meters = " + String(alt_meters));
  float alt_feet = alt_meters * 3.28084;
  return(alt_feet);
}

float pressure_sensor::read_temperature() {
  return(sensor.getTemperature(CELSIUS, ADC_512));
}
/*
void pressure_sensor::create_sensor(ms5803_addr _addr) {
  /* Create the sensor and initialize it
   *
   * Inputs
   * ------
   *  _addr: int representing the address of the sensor

  // TODO: test whether this correctly sets the sensor variable
  MS5803 sensor(_addr);
  initialize_sensor();
}*/

void pressure_sensor::initialize_sensor() {
  /* Initialize the sensor and print an error if it failed to initialize
   */
  sensor.reset();
  int counter = 0;
  while (sensor.begin() && counter < 5) {
    Serial.println("Pressure Sensor failed to initialize");
    sensor.reset();
    delay(500);
    counter++;
    if (counter == 5) {
      Serial.println("Pressure Sensor failed 5x, aborting!");
      // while(1);
    }
  } // end while
  Serial.println("Pressure Sensor initialized");
  set_baseline(sensor.getPressure(ADC_4096));
}

// get functions for each member variable
ms5803_addr pressure_sensor::get_addr() {return(addr);}

//MS5803& pressure_sensor::get_sensor() {return(sensor);}

float pressure_sensor::get_baseline() {return(baseline);}

// set functions for each member variable
void pressure_sensor::set_addr(ms5803_addr _addr) {
  addr = _addr;
}

void pressure_sensor::set_baseline(float _baseline) {
  baseline = _baseline;
}

// }}}

// IMU {{{
#define IMU_DEFAULT_TX 16
#define IMU_DEFAULT_RX 17

IMU::IMU(){
  /* Constructor, tests serial communication and initializes the data to 0
   */
  set_Data(0, 0, 0);
}

TextFinder finder(Serial2);
const int numOfFields = 3;
float Array[numOfFields];

int IMU::comms_Test() {
  /* Check communication between the IMU arduino and the main arduino
   *
   * Returns
   * -------
   *  int - 1 corresponds to sucess, 0 corresponds to failure
   */
  //int time = millis();
  //Serial2.begin(9600);
  Serial.println("In Communication Test");
  Serial2.print("#c");
  // check communication with IMU
  boolean found_CommsHeader = finder.find("C");

  if (found_CommsHeader) {
    Serial.println("Found Communication Header");
    float testVal = finder.getFloat();
    if (testVal == 2.0) {
      return(1);
    }
  }

  Serial.println("Did not Find Communication Header");

  return(0);
  /*while((millis()-time) < 180000){
    if(Serial2.read() == '1'){//need to change back to '1'
      Serial2.print('0');
      return(1);
    }
    Serial2.print('1');
    delay(500);
  }
  return(0);
  */
}

IMU_Data IMU::read_IMU(){
  /* Read current imu data for acceleration and direction
   *
   * Returns
   * -------
   *  IMU_Data - data corresponding to the current values on the IMU
   */
  Serial2.write("#f"); //request Data
  int fieldIndex = 0;
  boolean found_HeaderChar = finder.find("H");

  if(found_HeaderChar){
    while(fieldIndex < numOfFields){
      Array[fieldIndex++] = finder.getFloat();
    }
    set_Data(Array[0], Array[1], Array[2]);
    Serial.println("IMU Received Data");
    Serial.println(String(Array[0]) + ", " +  String(Array[1]) + ", " + String(Array[2]));
  }

  //bool reading = false;
  //String receivedValues = "";
  //String delimiter = ",";
  //float numbers[3] = {0.0,0.0,0.0};
  //int numIdx=0;
  /*
  int time = millis();
  //Request Data
  Serial2.print('2');
  Serial.println("Inside read_IMU");
  while((millis()-time) < 180000) {
    if (Serial2.available() > 0) {
      Serial.println((char)Serial2.read());
      /*if(Serial2.read() == '<') {
        numbers[0] = Serial2.readStringUntil(',').toFloat();
        numbers[1] = Serial2.readStringUntil(',').toFloat();
        numbers[2] = Serial2.readStringUntil('>').toFloat();
        set_Data(numbers[0], numbers[1], numbers[2]);
        Serial2.print('0');
        return(get_Data());
      } else {
        delay(500);
      }
    } else {
      Serial2.print('2');
    }
  }*/
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

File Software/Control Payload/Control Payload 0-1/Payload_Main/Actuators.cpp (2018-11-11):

#include "Actuators.h"

Servo HeliumServo;
#define BallastPin 6

void setup_Actuators(void) {
  HeliumServo.attach(7);
  HeliumServo.write(HeliumStartAngle);
  pinMode(BallastPin, OUTPUT);
  digitalWrite(BallastPin, 0);
}

// Open helium vent by given percentage (0-1) for a given time period
void openHeliumServo (struct Helium_Data* data, float percentOpen) {
  data->position = percentOpen;
  double degree;
  if (!data->open) {
    data->open = true;
  }
  percentOpen = percentOpen * 2;
  if (percentOpen <= 1) {
    degree = 180 * asin(percentOpen) / PI;
  } else {
    degree = 180 * asin(percentOpen - 1) / PI + 90;
  }
  HeliumServo.write(HeliumStartAngle + degree);
}

void closeHeliumServo (struct Helium_Data* data) {
  data->position = 0;
  HeliumServo.write(HeliumStartAngle);
  data->open = false;
  data->ventTime = millis();
}

void oscillateHeliumServo (struct Helium_Data* data, int period, int repetitions, int degree) {
  if (!data->open) {
    for (int i; i < repetitions; i++) {
      HeliumServo.write(HeliumStartAngle + degree);
      delay(period);
      HeliumServo.write(HeliumStartAngle);
    }
  } else {
    float start_position = data->position;
    HeliumServo.write(HeliumStartAngle);
    for (int i; i < repetitions; i++) {
      HeliumServo.write(HeliumStartAngle + degree);
      delay(period);
      HeliumServo.write(HeliumStartAngle);
    }
    openHeliumServo ( data, start_position);
  }
}

void runBallastServo (void) {
  analogWrite(BallastPin, 243);
  delay(200);

  analogWrite(BallastPin, 193);
  delay(400);

  analogWrite(BallastPin, 154);
  delay(100);

  digitalWrite(BallastPin, 0);
  delay(500);
}

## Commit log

2018-07-23 Initial Commit of Files
    [Avionics_Main_Board.brd, Avionics_Main_Board.sch, Faceplate.stl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]
2018-08-10 Modifications to Spinner
    [Avionics_Main_Board.sch, Faceplate.stl, Hopper.stl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]
2018-08-10 Added new header file and code for sensors
    Added Actuators header and cpp. Wrote logic for temperature and pressure transmitters.
2018-08-14 Code and Schematic Updates
    Added State Machine .h & .cpp file
    Added Resistor to LM335 and added battery voltage measurement to schematic.
    Board Layout TBD
    [Avionics_Main_Board.brd, Avionics_Main_Board.sch]
2018-08-21 Initial IMU Code
    setup_IMU_01
    -start and check communication with IMU
    - enable orientation and accelerometer/gyroscope quaternion outputs
    read_IMU_01
    - update values and return magnetometer and quaternion values
    defined IMU_OUTPUT struct to store IMU data
2018-08-21 Update Sensors Files
    Small bugfix for return type of read_PIT_01
    Added function descriptions using numpy docstrings style
    Added TODOC codetags where more explanation is needed
    Added FIXME codetags where I see potential issues
    * Most notable: global variable usage
    [Sensors.cpp, Sensors.h]
2018-08-22 Add Include Guards to .h Files
    Added include guards to all .h files
    Added a missing ; on IMU_OUTPUT struct definition
    [Communications.h, Sensors.h]
2018-08-24 Fix Sensors.h IMU function declarations
    Original type for read_IMU_01 was void, replaced with IMU_OUTPUT. This
    required moving the IMU_OUTPUT struct declaration before the function
    declaration.
    Added a comment describing the elements contained in the IMU_OUTPUT
    struct.
    [Sensors.h]
2018-08-26 Updated 3D Printed files
    [Faceplate.stl, Hopper.stl, Spinner.stl]
2018-08-30 IMU code structure updates
    -new folder for imu code
    -moved code for setup and reading
2018-09-03 Schematic Rev C and CAD Files changes
    Completed rev C of hardware schematic
    Created new PCB layout
    Updated tolerance on ballast dispenser
    [Avionics_Main_Board.brd, Avionics_Main_Board.sch, Faceplate.stl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]
2018-09-06 Add basic altitude control system
    Created a method for determining when to drop ballast or release helium
    based on current altitude, velocity, and acceleration
    Updated Control.h to reflect the changes made to Control.cpp
    Updated Payload_Main.ino to reflect the changes made to Control.h
2018-09-06 Add velocity and acceleration thresholds
    Added a set_rates function which adjusts the minimum velocity and
    acceleration values that are considered "fast enough"
    Updated the altitude_control function to use the new threshold values
    instead of 0
    Updated the min and max altitudes to use floats instead of integers
    Updated Control.h to reflect the new set_rates function
2018-09-07 Control control code to OOP
    The control algorithm uses an altitude range, as well as thresholds for
    velocity and acceleration in addition to methods to control altitude.
    This lends itself to using a class instead of multiple global variables
    and separate functions.
    Updated Control.h and Control.cpp to use OOP styles
    Moved old Control.h and Control.cpp to *.bak temporarily
2018-09-09 Added Matlab Code
    Flight fimulation and a matlab framework for sending and receiving iridium messages through email.
2018-09-10 Changes to IMU code
    - Determining orientaiton
    - Projecting acceleration data
    - Determining how much accleration is "up"
2018-09-13 Replace temperature sensor with a class
    Replaced the existing temperature sensor code to contain all
    interactions and required variables within a class.
    [Sensors.cpp, Sensors.h]
2018-09-13 correct firmware for imu
    - calculate roll pitch yaw
    - calculate vertical acceleration
    - need to clean up code
    [IMU.ino]
2018-09-13 Add class for pressure sensor
    Combined pressure variables and methods into a class. The temperature
    sensor class can be initialized either using the default address of
    sensor 1, an address, or an MS5803 sensor object.
2018-09-14 Horizontal acceleration and direction with relation to north
    - added code to determine horizontal acceration through rotation matrix and projection onto the horizontal plane
    - added code to determine direction with respect to the calibration value (should calibrate so that +x -> N
    -cleaned up code
2018-09-14 Create GPS class
    Replaced all GPS related functionality with a class.
    Created a struct to contain all GPS data for easier access.
    [Sensors.cpp, Sensors.h]
2018-09-17 Update to Comm code
    Fixed issues preventing communications code from compiling
    [Communications.cpp, Communications.h]
2018-09-17 GUI Mockup
    - created GUI mockup
    - does not currently have functionality
    - need to finalize communication code before adding major functionality
2018-09-20 Update control algorithm
    Added parameter weights for calculating the amount of ballast and
    helium to release.
    Adjusted algorithm to use delta altitude, velocity, and acceleration
    Provided access to adjust parameter weights in real time
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2018-10-05 communication with IMU
    - addition of IMU class to sensors.cpp/.h
    - functions to check communication with IMU
    - read data from IMU
    - write data to arduino via serial ports
    - delete functions from main that are not going to be used
2018-10-05 Add altidude calculation to pressure sensor
    Updated the pressure sensor class to include an altitude calculation
    from the baseline.
2018-10-05 Document and update IMU code in Sensors.cpp(.h)
    Added comment blocks to the IMU sensor code to describe functionality.
    Updated the IMU's set_data function to take 3 floats instead of 1
    IMU_Data struct as inputs.
    Created global sensor objects in the main file.
    Read sensor data every iteration of the main loop.
2018-10-11 Writing main loop
    - check current conditions every 5 seconds
    - post processing of conditions (velocity, altitude calculation)
    - run control code every 5 minutes
    - check for manual/automatic mode
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2018-10-16 More hardware changes
    [Bracket.stl, Faceplate.stl, Fitting.stl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]
2018-10-16 Electrical board changes
    [Avionics_Main_Board.brd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]
2018-10-25 Edits to fix compilation errors
    - pressure sensors work with this code
    - commented out other sensors
    - need to fix serial prints in constructors
    - fixed pressure sensor addresses
    [Payload_Main.ino, Sensors.cpp, Sensors.h]
2018-10-25 Remove print statements from constructors
    Constructors were being called before Serial was started, so the print
    statements were failing silently. They were moved to an
    initialize/create function for each sensor to prevent silent failures.
    [Payload_Main.ino, Sensors.cpp]
2018-10-29 Update to Communications
    Fixed encode/decode functions and added new GUI base
    [Communications.cpp, Communications.h]
2018-10-30 IMU code edits
    - fixed any imu errors
    - added back in commented out imu code
    [IMU.ino, Payload_Main.ino, Sensors.cpp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]
2018-10-30 Revert "Updates to Communication Code"
    This reverts commit 763171ca68bc404786de4f55b44db6b98ac5d0e6, reversing
    changes made to 7ea76f73f2e98c81bf0a484f4f251ebee1ff95d2.
    [Actuators.cpp, Communications.cpp, Communications.h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]
2018-10-31 Communication Update
    Fixes to communication code
    [Communications.cpp, Communications.h]
2018-11-01 Update IMU serial communication
    Existing communication between the arduino was faulty, so it was replaced with a new communication method.
    The IMU firmware needs to be updated to reflect these changes.
    [Sensors.cpp]
2018-11-01 Update IMU firmware for new communication method
    Add communication code to the IMU firmware to communicate with the
    Arduino
    Add comms test functionality to the IMU firmware to confirm
    communication status
2018-11-01 Update sensor and IMU code to compile
    Small syntax errors in IMU and sensors.cpp were fixed
    Communications was temporarily commented out due to significant
    compilation errors
    [Communications.cpp, Communications.h, IMU.ino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]
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2018-11-10 Electronics and Hardware changes
    [Avionics_Main_Board.brd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]
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2018-11-10 Added ground for IMU
    [Avionics_Main_Board.brd]
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2018-11-11 11-11 update
    Temp change and communications fix
    [Communications.cpp, Communications.h, Payload_Main.ino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]
2018-11-11 Add temperature measurements from pressure sensor
    Temperature sensor was giving incorrect data, so it was replaced with temperature data from the pressure sensor.
    [Payload_Main.ino, Sensors.cpp, Sensors.h]
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2018-12-03 Added flight data
    [FlightData.xlsx]

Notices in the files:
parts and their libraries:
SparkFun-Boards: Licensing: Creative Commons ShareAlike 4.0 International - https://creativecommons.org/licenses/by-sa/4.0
